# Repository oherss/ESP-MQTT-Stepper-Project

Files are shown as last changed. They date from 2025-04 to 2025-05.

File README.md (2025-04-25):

# ESP MQTT Stepper Project

This project is an integration between the TMC 2209 stepper driver with an ESP 32-S3 chip and code that allows the motor to connect via MQTT with a custom protocol.
The code parts of this project are made to be compatible with the PD Stepper hardware project.
The hardware is also inspired by this project, but without some of the extra bells and whistles, like PD power, expansion ports and buttons.

# This is a student project
Which means I am doing this for an exam and may not maintain this repo in the future, this is mostly a proof-of-concept.
This also means the directories may be kind of confusing, and there is also some extra code in here for an unrelated project, so don't mind my mess :)

# Hardware
The hardware, just like the PD-Stepper project is meant to be attached to the back of an ordinary Nema 17 stepper motor.
# PCB
As mentioned, this is based on the PD-Stepper project, but with just the essentials, mostly to make it cheaper to produce.
This means we still get the TMC 2209 silent stepper motor driver, and the flexible ESP-32-s3 microprocessor, but I have done away with the I2C and AUX port, USB-C Power Delivery and I have also replaced the unobtainum power-regulator (MPM-3612-33) and replaced it with a commonplace alternative.
In the PCB folder I have both the fabrication files, complete with BOM and assemply files, so you don't need to solder the components yourself.
The files have been prepared for them to be produced via JLC-PCB, so if you want to use another fabricator, the files may not work.
There is also the project files for KiCAD 7.0 files to work on the schematic if you'd like, although I have a few components with custom libraries, which might make it annoying to initially set up.
# Other Hardware
In the future I'd like to get some 3D-models for 3D-printing,so one could incase the driver on the back of the stepper motor. And more importantly, I'd like a insulation plate between the PCB and back of the motor, to avoid short-circuits.
I'd also like to make plans for a cable to connect the motor to the PCB, like there is included with the PD-Stepper.

# Software
I have 2 versions of the code for the stepper motor driver, but they are in very different states of development, the basic version was the first draft, to test the capabilities.
The advanced uses the serial communication with the driver, but also has many updates on the protocol, so I would generally reccomend that version.

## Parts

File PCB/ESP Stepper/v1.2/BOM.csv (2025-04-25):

Id | Designator | Footprint | Quantity | Comment | Supplier and ref
1 | U2 | QFN28_5X5_3X8_EPAD_TRI | 1 | TMC2209-LA-T
2 | U1 | SOT-223-3_TabPin2 | 1 | AMS1117-3.3
3 | C7,C4,C3,C2 | Capacitor 0805 | 4 | C 100n
4 | R12,R10 | R_0603_1608Metric | 2 | R 10k
5 | R9,R8 | R_1206_3216Metric | 2 | R 100m
6 | C6 | C 0603 | 1 | C 10μf
7 | C14 | Capacitor 0805 | 1 | C 1uf
8 | J4 | JST_EH_B4B-EH-A_1x04_P2.50mm_Vertical | 1 | Conn_01x04_Socket
9 | R11 | R_0603_1608Metric | 1 | R 4.7k
10 | C13 | Capacitor 0805 | 1 | C 0.1μf
11 | R2,R1 | R_0603_1608Metric | 2 | R 5.1K
12 | D5 | LED_0603_1608Metric | 1 | MQTT
13 | U3 | XCVR_ESP32-S3-MINI-1-N8 | 1 | ESP32-S3-MINI-1-N8
14 | SW2,SW1 | SW_PTS810_SJM_250_SMTR_LFS | 2 | SW_Push
15 | R3 | R_2512_6332Metric | 1 | R 10
16 | R15 | R_0603_1608Metric | 1 | R 2k
17 | D3 | LED_0603_1608Metric | 1 | PWR
18 | D4 | LED_0603_1608Metric | 1 | WiFi
19 | R14,R13,R4 | R_0603_1608Metric | 3 | R 1k
20 | J1 | USB_C_Receptacle_G-Switch_GT-USB-7010ASV | 1 | USB_C_Receptacle_USB2.0
21 | D2,D1 | TVS_LESD5D5.0CT1G | 2 | LESD5D5.0CT1G
22 | C1 | CP_Elec_6.3x7.7 | 1 | C 100μf
23 | C8 | Capacitor 0805 | 1 | C 0.1uf
24 | C5 | Capacitor 0402 | 1 | C 22n

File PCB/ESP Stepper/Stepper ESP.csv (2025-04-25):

# | Reference | Qty | Value | Footprint | DNP
1 | C1 | 1 | C 100μf | Capacitor_SMD:CP_Elec_6.3x7.7
2 | C2, C3, C4, C7 | 4 | C 100n | ExtraModulesSproxx:Capacitor 0805
3 | C5 | 1 | C 22n | ExtraModulesSproxx:Capacitor 0402
4 | C6 | 1 | C 10μf | ExtraModulesSproxx:C 0603
5 | C8, C9, C12 | 3 | C 0.1uf | ExtraModulesSproxx:Capacitor 0805
6 | C10, C11 | 2 | C 22uf | ExtraModulesSproxx:Capacitor 0402
7 | C13 | 1 | C 0.1μf | ExtraModulesSproxx:Capacitor 0805
8 | C14 | 1 | C 1uf | ExtraModulesSproxx:Capacitor 0805
9 | D1, D2 | 2 | LESD5D5.0CT1G | ExtraModulesSproxx:TVS_LESD5D5.0CT1G
10 | D3 | 1 | PWR | LED_SMD:LED_0603_1608Metric
11 | D4 | 1 | WiFi | LED_SMD:LED_0603_1608Metric
12 | D5 | 1 | MQTT | LED_SMD:LED_0603_1608Metric
13 | J1 | 1 | USB_C_Receptacle_USB2.0 | Connector_USB:USB_C_Receptacle_G-Switch_GT-USB-7010ASV
14 | J4 | 1 | Conn_01x04_Socket | Connector_JST:JST_EH_B4B-EH-A_1x04_P2.50mm_Vertical
15 | R1, R2 | 2 | R 5.1K | Resistor_SMD:R_0603_1608Metric
16 | R3 | 1 | R 10 | Resistor_SMD:R_2512_6332Metric
17 | R4, R13, R14 | 3 | R 1k | Resistor_SMD:R_0603_1608Metric
18 | R5, R6 | 2 | R 100k | Resistor_SMD:R_0603_1608Metric
19 | R7, R10, R12 | 3 | R 10k | Resistor_SMD:R_0603_1608Metric
20 | R8, R9 | 2 | R 100m | Resistor_SMD:R_1206_3216Metric
21 | R11 | 1 | R 4.7k | Resistor_SMD:R_0603_1608Metric
22 | R15 | 1 | R 2k | Resistor_SMD:R_0603_1608Metric
23 | SW1, SW2 | 2 | SW_Push | ExtraModulesSproxx:SW_PTS810_SJM_250_SMTR_LFS
24 | U2 | 1 | TMC2209-LA-T | QFN28_5X5_3X8_EPAD_TRI
25 | U3 | 1 | ESP32-S3-MINI-1-N8 | ExtraModulesSproxx:XCVR_ESP32-S3-MINI-1-N8
26 | U4 | 1 | MPM3612-33 | LGA_MPM3612_MNP

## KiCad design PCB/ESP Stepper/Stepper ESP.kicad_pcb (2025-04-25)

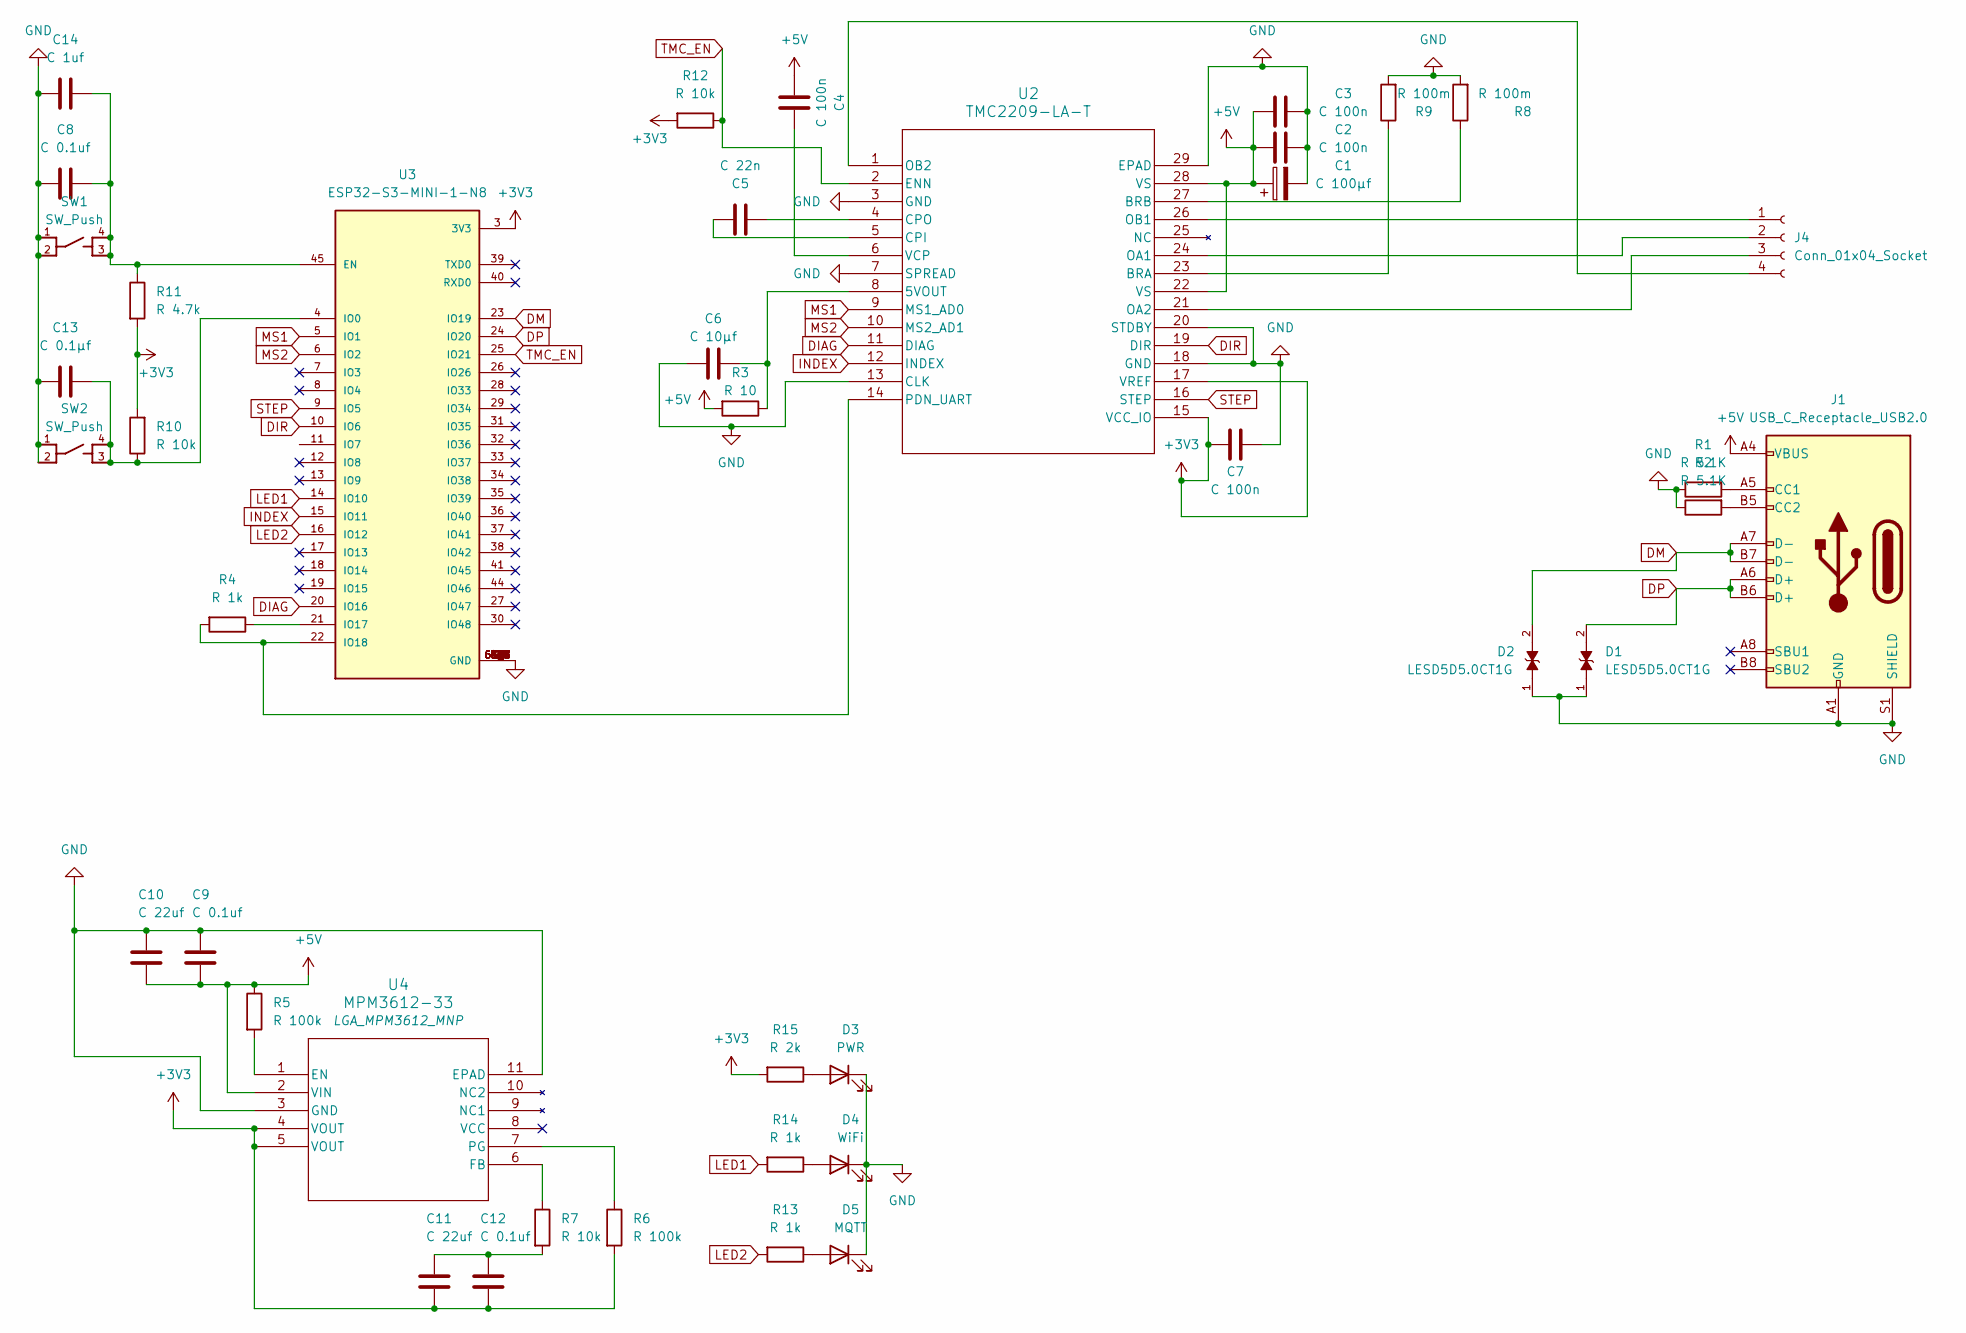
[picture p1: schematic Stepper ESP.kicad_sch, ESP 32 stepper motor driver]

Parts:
C1: C 100μf; CP_Elec_6.3x7.7
C2, C3, C4, C7: C 100n; Capacitor 0805
C5: C 22n; Capacitor 0402
C6: C 10μf; C 0603
C8, C9, C12: C 0.1uf; Capacitor 0805
C10, C11: C 22uf; Capacitor 0402
C13: C 0.1μf; Capacitor 0805
C14: C 1uf; Capacitor 0805
D1, D2: LESD5D5.0CT1G; TVS_LESD5D5.0CT1G; PARTREV O
D3: PWR; LED_0603_1608Metric
D4: WiFi; LED_0603_1608Metric
D5: MQTT; LED_0603_1608Metric
J1: USB_C_Receptacle_USB2.0; USB_C_Receptacle_G-Switch_GT-USB-7010ASV
J4: Conn_01x04_Socket; JST_EH_B4B-EH-A_1x04_P2.50mm_Vertical
R1, R2: R 5.1K; R_0603_1608Metric
R3: R 10; R_2512_6332Metric
R4, R13, R14: R 1k; R_0603_1608Metric
R5, R6: R 100k; R_0603_1608Metric
R7, R10, R12: R 10k; R_0603_1608Metric
R8, R9: R 100m; R_1206_3216Metric
R11: R 4.7k; R_0603_1608Metric
R15: R 2k; R_0603_1608Metric
SW1, SW2: SW_Push; SW_PTS810_SJM_250_SMTR_LFS
U2: TMC2209-LA-T; QFN28_5X5_3X8_EPAD_TRI
U3: ESP32-S3-MINI-1-N8; XCVR_ESP32-S3-MINI-1-N8; PARTREV v0.6
U4: MPM3612-33; LGA_MPM3612_MNP

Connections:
+3V3: C7.2, C11.2, C12.2, R6.2, R10.2, R11.2, R12.2, R15.2, U2.15 (VCC_IO), U2.17 (VREF), U3.3 (3V3), U4.4 (VOUT), U4.5 (VOUT)
+5V: C1.1, C2.2, C3.2, C4.2, C9.2, C10.2, J1.A4 (VBUS), J1.A9 (VBUS), J1.B4 (VBUS), J1.B9 (VBUS), R3.2, R5.1, U2.22 (VS), U2.28 (VS), U4.2 (VIN)
DIAG: U2.11 (DIAG), U3.20 (IO16)
DIR: U2.19 (DIR), U3.10 (IO6)
DM: D2.2, J1.A7 (D-), J1.B7 (D-), U3.23 (IO19)
DP: D1.2, J1.A6 (D+), J1.B6 (D+), U3.24 (IO20)
GND: C1.2, C2.1, C3.1, C6.2, C7.1, C8.2, C9.1, C10.1, C13.2, C14.2, D1.1, D2.1, D3.1 (K), D4.1 (K), D5.1 (K), J1.A1 (GND), J1.A12 (GND), J1.B1 (GND), J1.B12 (GND), J1.S1 (SHIELD), R1.1, R2.1, R8.2, R9.2, SW1.1, SW1.2, SW2.1, SW2.2, U2.3 (GND), U2.7 (SPREAD), U2.13 (CLK), U2.18 (GND), U2.20 (STDBY), U2.29 (EPAD), U3.1 (GND), U3.2 (GND), U3.42 (GND), U3.43 (GND), U3.46 (GND), U3.47 (GND), U3.48 (GND), U3.49 (GND), U3.50 (GND), U3.51 (GND), U3.52 (GND), U3.53 (GND), U3.54 (GND), U3.55 (GND), U3.56 (GND), U3.57 (GND), U3.58 (GND), U3.59 (GND), U3.60 (GND), U3.61 (GND), U3.61_1 (GND), U3.61_2 (GND), U3.61_3 (GND), U3.61_4 (GND), U3.61_5 (GND), U3.61_6 (GND), U3.61_7 (GND), U3.61_8 (GND), U3.62 (GND), U3.63 (GND), U3.64 (GND), U3.65 (GND), U4.3 (GND), U4.11 (EPAD)
INDEX: U2.12 (INDEX), U3.15 (IO11)
LED1: R14.2, U3.14 (IO10)
LED2: R13.2, U3.16 (IO12)
MS1: U2.9 (MS1_AD0), U3.5 (IO1)
MS2: U2.10 (MS2_AD1), U3.6 (IO2)
unnamed: C11.1, C12.1, R7.2
unnamed: D3.2 (A), R15.1
unnamed: D4.2 (A), R14.1
unnamed: D5.2 (A), R13.1
unnamed: J1.A5 (CC1), R1.2
unnamed: J1.B5 (CC2), R2.2
unnamed: J4.1, U2.26 (OB1)
unnamed: J4.2, U2.24 (OA1)
unnamed: J4.3, U2.21 (OA2)
unnamed: J4.4, U2.1 (OB2)
unnamed: C6.1, R3.1, U2.8 (5VOUT)
unnamed: R9.1, U2.23 (BRA)
unnamed: R8.1, U2.27 (BRB)
unnamed: C5.1, U2.5 (CPI)
unnamed: C5.2, U2.4 (CPO)
unnamed: R4.2, U2.14 (PDN_UART), U3.22 (IO18)
unnamed: C4.1, U2.6 (VCP)
unnamed: C8.1, C14.1, R11.1, SW1.3, SW1.4, U3.45 (EN)
unnamed: C13.1, R10.1, SW2.3, SW2.4, U3.4 (IO0)
unnamed: R4.1, U3.21 (IO17)
unnamed: R5.2, U4.1 (EN)
unnamed: R7.1, U4.6 (FB)
unnamed: R6.1, U4.7 (PG)
STEP: U2.16 (STEP), U3.9 (IO5)
TMC_EN: R12.1, U2.2 (ENN), U3.25 (IO21)

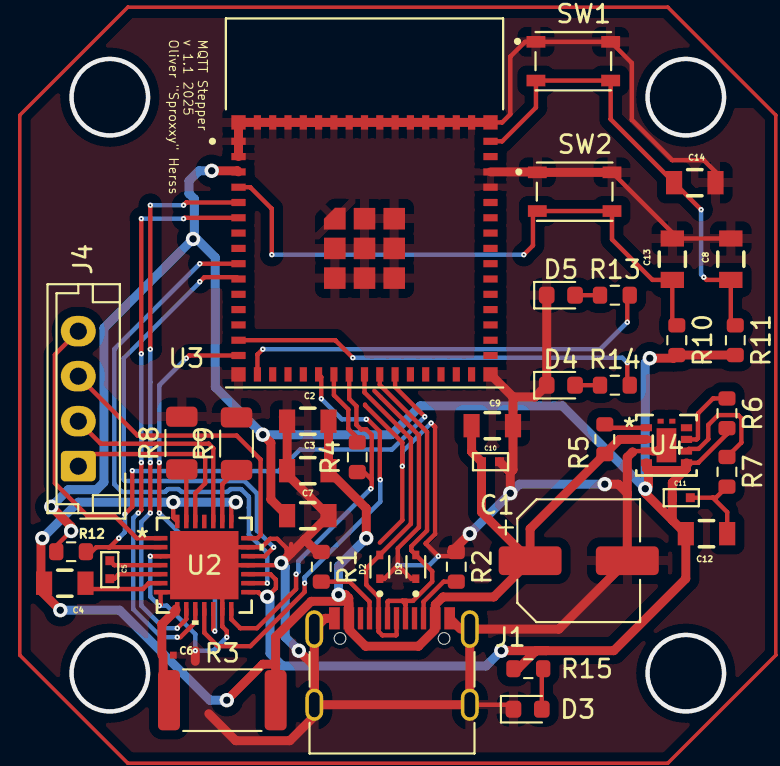
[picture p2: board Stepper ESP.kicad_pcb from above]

Board: 2 copper layers, 41 parts (0 on the bottom side), 37 nets.

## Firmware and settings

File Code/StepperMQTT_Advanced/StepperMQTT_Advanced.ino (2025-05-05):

/*
 MQTT connected stepper motor firmware developed for Simmoe by Oliver "Sproxxy" Herss March 2025 based on the PD stepper project.

 Make sure to have the ESP-32 boards in your IDE to build for the hardware.
*/

#include <WiFi.h>
#include <PubSubClient.h>
#include <ArduinoJson.h>
#include <TMC2209.h>

/////////////////////////
//    WiFi Details     //
/////////////////////////

const char* ssid = "Next-Iot";
const char* password = "shin-pygmy-renal-Hahk";

/////////////////////////
//     MQTT Server     //
/////////////////////////

const char* mqtt_server = "mqtt-plain.nextservices.dk";
uint16_t mqtt_port = 1883;
const int motor_id = 1;





//TMC2209 setup
TMC2209 stepper_driver;
HardwareSerial & serial_stream = Serial2;
const long SERIAL_BAUD_RATE = 115200;

const uint8_t RUN_CURRENT_PERCENT = 100; //how much current to run at (0-100%)

/////////////////////////
//     Pin Defines     //
/////////////////////////

//TMC2209 Stepper Driver
#define TMC_EN  21 //Low to enable motor, high to disable)
#define STEP    5
#define DIR     6
#define MS1     1
#define MS2     2
#define SPREAD  7
#define TMC_TX  17
#define TMC_RX  18
#define DIAG    16
#define INDEX   11

//PD Trigger (CH224K)
#define CFG1    38
#define CFG2    48
#define CFG3    47

//Other
#define VBUS    4
#define NTC     7
#define LED1    10
#define LED2    12

/////////////////////////////
// Global Variable Defines //
/////////////////////////////

//Motor speeds
int delays[] = {15, 2000, 1000, 700, 400, 200, 100, 75, 50, 40, 30}; //list of speeds (higher = slower, 0 = stop)
int numSpeeds = 10;


//MQTT topic
String MQTTTopic = "ESPStepper";
String MQTTTopicAnnounce = "Pairing";

//MQTT subtopics for specific motor ID
String sendTopic;
String recieveTopic;
String clientTopic;
String serverTopic;

//combined MQTT message
String MQTTmsg = "";
String DeviceMessage;

// Extracted JSON parameters from message
int Steps = 0;
int Speed = 0;
int Dir = 0;
int microSteps = 256; //Standard value

//WiFi
WiFiClient espClient;

//MQTT function variables
PubSubClient client(espClient);
unsigned long lastMsg = 0;
#define MSG_BUFFER_SIZE	(50)
char msg[MSG_BUFFER_SIZE];

void setup_wifi() {// Wifi setup
  delay(10);
  // We start by connecting to a WiFi network
  Serial.println();
  Serial.print("Connecting to ");
  Serial.println(ssid);

  //WiFi connection established
  WiFi.mode(WIFI_STA);
  WiFi.begin(ssid, password);

  while (WiFi.status() != WL_CONNECTED) { //Whie connecting blink LED to show status
    delay(250);
    Serial.print(".");
    digitalWrite(LED1, HIGH);
    delay(250);
    digitalWrite(LED1,LOW);
  }

  //Show that WiFi connection was sucessful via serial, and show the current IP adress
  Serial.println("");
  Serial.println("WiFi connected");
  Serial.println("IP address: ");
  Serial.println(WiFi.localIP());
}

void callback(char* topic, byte* payload, unsigned int length) { //Runs whenever we receive a message on the recive a message on subsribed topics
  //recieve message and print topic to serial monitor
  Serial.print("Message arrived [");
  Serial.print(topic);
  Serial.print("] ");

  //combines characters into full string
  MQTTmsg = ""; //clear the string
  for (int i = 0; i < length; i++) {
    MQTTmsg += (char)payload[i];
  }

  //prints received message to console
  Serial.println(MQTTmsg);

  if(String(topic) == recieveTopic){ //Checks if message is in the command topic
    StaticJsonDocument<200> doc;  // Define a JSON document with a suitable size
    DeserializationError error = deserializeJson(doc, MQTTmsg); //interpret JSON from received message

    if (error) { //Prints JSON error to console and via MQTT to user
        Serial.print("deserializeJson() failed: ");
        Serial.println(error.f_str());
        String messageToSend = "Json parse failed: " + String(error.f_str());
        client.publish(sendTopic.c_str(),  messageToSend.c_str());
        return;
      }

    String StepString = doc["Steps"]; //Store the data in "Steps" as a string for comparison 

    if(StepString == "Run"){ //check if constant motion is requested
      Speed = doc["Speed"];
      Dir = doc["Dir"];
      microSteps = doc["MicroSteps"];

      if (Dir == 1){ //set direction
        digitalWrite(DIR, HIGH);
      } else {
        digitalWrite(DIR, LOW);
        Speed = -Speed;
      }

      String stringToSend = "Running motor at speed: " + String(Speed) + " at " + String(microSteps) + " microsteps";
      Speed *= 70; //Scale speed to value stepper driver can understand
      digitalWrite(TMC_EN, LOW);
      stepper_driver.setMicrostepsPerStep(microSteps);
      stepper_driver.enable();
      stepper_driver.moveAtVelocity(Speed*microSteps); //Starts motion
      Serial.println(stringToSend);
      client.publish(sendTopic.c_str(), stringToSend.c_str()); //Sends info back to user via MQTT
    }

    else if(StepString == "Stop"){ //Check if command is to stop constant motion
      //digitalWrite(TMC_EN, HIGH);
      stepper_driver.moveAtVelocity(0);
      stepper_driver.disable();
      Serial.println("Motor stopped");
      client.publish(sendTopic.c_str(),  "Motor stopped");
    }

    else{ //If not constant motion, intepret amount of steps requested, and run the doSteps() function
      Steps = doc["Steps"];  // Assuming the JSON contains a parameter named "Steps"
      Speed = doc["Speed"];  // Assuming the JSON contains a parameter named "Speed"
      Dir = doc["Dir"];  // Assuming the JSON contains a parameter named "Dir"
      microSteps = doc["MicroSteps"]; // Assuming the JSON contains a parameter named "MicroSteps"
      stepper_driver.setMicrostepsPerStep(microSteps); //Sets micro step resolution
      doSteps(Dir, Steps, Speed); //Runs function for moving the motor
    }

  }

  else{ //If recieved message is not a command, assume it is a pairing command, and send out device info
    Serial.println("Sending device info on topic: " + clientTopic);
    client.publish(clientTopic.c_str(), DeviceMessage.c_str());
  }
}

void reconnect() { //MQTT connection to server
  // Loop until we're connected
  while (!client.connected()) {
    Serial.print("Attempting MQTT connection...");
    // Attempt to connect
    if (client.connect(MQTTTopic.c_str())) {
      Serial.println("connected");
      // Once connected, publish an announcement...
      client.publish(sendTopic.c_str(), "Motor Online");
      Serial.print("Response topic: ");
      Serial.println(sendTopic);
      // ... and resubscribe
      client.subscribe(recieveTopic.c_str());
      client.subscribe(serverTopic.c_str());
      Serial.print("Subscribed to topic: ");
      Serial.println(recieveTopic);
      Serial.print("Subscribed to topic: ");
      Serial.println(serverTopic);
    } else { // If we fail to connect to MQTT server
      Serial.print("failed, rc=");
      Serial.print(client.state());
      Serial.println(" try again in 5 seconds");
      // Wait 5 seconds before retrying
      delay(5000);
    }
  }
}

void setup() {
  pinMode(LED1, OUTPUT); //WiFi status LED
  pinMode(LED2, OUTPUT); //MQTT status LED
  
    //PD Trigger Setup  (Selects the voltage needed over the USB port, tín this case just 5 volts)
  pinMode(CFG1, OUTPUT);
  pinMode(CFG2, OUTPUT);
  pinMode(CFG3, OUTPUT);
                            //  5V   9V   12V   15V   20V  (Can also be changed on the fly)
  digitalWrite(CFG1, HIGH); //  1    0     0     0     0
  digitalWrite(CFG2, LOW);  //  -    0     0     1     1
  digitalWrite(CFG3, LOW);  //  -    0     1     1     0
  
   //Setup serial comms with TMC2209
  pinMode(MS1, OUTPUT); 
  pinMode(MS2, OUTPUT); 
  pinMode(STEP, OUTPUT);
  pinMode(DIR, OUTPUT);
  pinMode(TMC_EN, OUTPUT);
  pinMode(DIAG, INPUT); //Response data pin from stepper driver

  //Motor setup
  digitalWrite(TMC_EN, LOW); //Enabled here and later enabled/disabled over UART

  digitalWrite(MS1, LOW); //used to set serial address in UART mode
  digitalWrite(MS2, LOW);


  digitalWrite(LED1, LOW);
  digitalWrite(LED2, LOW);


  stepper_driver.setup(serial_stream, SERIAL_BAUD_RATE, TMC2209::SERIAL_ADDRESS_0, TMC_RX, TMC_TX); //Sets up serial communication with stepper driver from defnied values
  stepper_driver.setRunCurrent(RUN_CURRENT_PERCENT); // sets motor current to defined value at the top of the code
  stepper_driver.enableAutomaticCurrentScaling(); //current control mode
  stepper_driver.enableStealthChop(); //stealth chop needs to be enabled for stall detect
  stepper_driver.setStandstillMode(stepper_driver.NORMAL);
  stepper_driver.disable(); //Disable the motor 


  //MQTT topics defines
  MQTTTopic += String(motor_id); //combines the name of the motor with its ID to make a unique device on MQTT
  sendTopic = MQTTTopic + "/Response"; //A subtopic for sending feedback on the motor's status
  recieveTopic = MQTTTopic + "/Motor"; //A subtopic the motor will listen to 
  clientTopic = MQTTTopicAnnounce + "/Client"; //A subtopic for sending information about the device upon bootup and upon request
  serverTopic = MQTTTopicAnnounce + "/Server"; //A subtopic the motor will listen to to send info about itself to the client topic
  DeviceMessage = "{ResponseTopic: " + sendTopic + ", CommandTopic: " + recieveTopic + ", ID: " + motor_id + ", DeviceType: Stepper_Motor, MinSpeed: 1, MaxSpeed: 10, MaxMicroSteps: 256}"; //The message the device sends during pairing
  
  //Start preparation code
  delay(500); //delay needed before "Serial.begin" to ensure bootloader mode entered correctly.
  Serial.begin(115200); //Start serial connection for debugging at set baud rate
  Serial.println("Code Starting");
  setup_wifi(); //Connect to WiFi
  client.setServer(mqtt_server, mqtt_port); //Define MQTT server attributes
  client.setCallback(callback); //Sets callback function when something arrives on the topic we have subscribed to
  reconnect(); //Connect to the MQTT server
}

void loop() {

  if (!client.connected()) { //check if MQTT connection is still good
    reconnect(); //recoonect if connection is bad
    digitalWrite(LED2, LOW); //Show MQTT bad status by turning off the corrosponding LED
    delay(1000);
  }
  else{
    digitalWrite(LED2, HIGH); //Show MQTT good status by turning on the corrosponding LED
  }

  if(WiFi.status() != WL_CONNECTED){ //check if WiFi connection is still good
    digitalWrite(LED1, LOW); //Show WiFi bad status by turning off the corrosponding LED
  }
  else{
    digitalWrite(LED1, HIGH); //Show WiFi good status by turning on the corrosponding LED
  }

  client.loop(); //MQTT loop
}

void doSteps (int DIRECTION, int STEPS, int STEPSPEED){
  STEPS *= microSteps;
  if(DIRECTION == 1 || DIRECTION == 0){ //Checks for valid direction
    if(STEPSPEED > 0 && STEPSPEED <= 10){ //checks for valid speed
      if(STEPS > 0){ //checks for valid amount of steps
        stepper_driver.enableCoolStep();
        stepper_driver.enable(); //enables motor
        int moveTime = ((STEPS * delays[STEPSPEED]) + (STEPS * delays[STEPSPEED])) / 1000000; //calculate the time it will take to complete any given motion from the parameters given
        String messageToSend = "{Steps: " + String(STEPS) + ", Speed: " + String(STEPSPEED) + ", TimeToFinish: " + String(moveTime) + ", Status: Running}"; //combined string with all the infor about requested motion and its status
        client.publish(sendTopic.c_str(),  messageToSend.c_str());

        if (DIRECTION == 1){ //set direction
            digitalWrite(DIR, HIGH);
          }
        else {
            digitalWrite(DIR, LOW);
          }

        for (int i = 0; i < STEPS; i++){ //For-loop for amount of steps to do
          digitalWrite(STEP, HIGH);
          delayMicroseconds(delays[STEPSPEED]);
          digitalWrite(STEP, LOW);
          delayMicroseconds(delays[STEPSPEED]);
        }

        messageToSend = "{Steps: " + String(STEPS) + ", Speed: " + String(STEPSPEED) + ", TimeToFinish: " + String(moveTime) + ", Status: Done}"; //combined string with all the infor about requested motion and its status
        client.publish(sendTopic.c_str(),  messageToSend.c_str());
      }
      else{
        client.publish(sendTopic.c_str(),  "Error in input: invalid steps, should be greater than 0");
        Serial.println("Error in input: invalid steps, should be greater than 0");
      }
    }
    else{
      client.publish(sendTopic.c_str(),  "Error in input: invalid speed (Range 1-10)");
      Serial.println("Error in input: invalid speed (Range 1-10)");
    }
  }
  else{
    client.publish(sendTopic.c_str(),  "Error in input: invalid direction, expected 1 (forward) or 0 (reverse)");
    Serial.println("Error in input: invalid direction, expected 1 (forward) or 0 (reverse)");
  }
  stepper_driver.disable();//disables motor
}
